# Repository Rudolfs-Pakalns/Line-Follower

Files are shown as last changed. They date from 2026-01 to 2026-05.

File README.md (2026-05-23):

# Line Follower

## This project contains code and resources for a line-following robot.

## Contents
- STM32 code for line-following robot
- KiCad schematic and PCB design files
- 3D model of the robot chassis
- Bill of Materials (BOM) for components used

[Line Follower Rules](https://robotuskola.lv/wp-content/uploads/2025/10/linefollower-rules-lv.pdf)

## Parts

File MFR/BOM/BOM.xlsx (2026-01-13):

N.p.k. | Detaļas numurs | Komponente / apraksts | Cena, par 1.gab, Eur | Skaits | Cena kopā, Eur | Tiešsaiste | Datasheet
1 | SUD50N04-8M8P-4GE3 | Power MOSFET, N Channel, 40 V, 50 A, 8800 µohm, TO-252 (DPAK), Surface Mount | 0.763 | 3 | 2.29 | farnell.lv (https://lv.farnell.com/vishay/sud50n04-8m8p-4ge3/mosfet-n-ch-40v-50a-to252/dp/1794799) | datasheet (https://4donline.ihs.com/images/VipMasterIC/IC/VISH/VISH-S-A0009485304/VISH-S-A0009485304-1.pdf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)
2 | BCX56 | Bipolar (BJT) Single Transistor, NPN, 80 V, 1 A, 500 mW, SOT-89, Surface Mount | 0.455 | 5 | 2.28 | farnell.lv (https://lv.farnell.com/multicomp-pro/bcx56/transistor-npn-1a-80v-sot89/dp/1798047) | datasheet (https://www.farnell.com/datasheets/2861630.pdf)
3 | QRE1113GR | Reflective Photo Interrupter, Phototransistor, SMD Gull Wing, 5 mm, 50 mA, 5 Vr, 1.2 Vf | 0.626 | 10 | 6.26 | farnell.lv (https://lv.farnell.com/onsemi/qre1113/photo-interrupter-reflective/dp/2322565) | datasheet (https://www.farnell.com/datasheets/2298118.pdf)
4 | BZD27C6V2P-E3-08 | Zener Single Diode, BZD, 6.2 V, 800 mW, DO-219AB, 2 Pins, 150 °C, Surface Mount | 0.191 | 5 | 0.96 | farnell.lv (https://lv.farnell.com/vishay/bzd27c6v2p-e3-08/zener-diode-0-8w-6-2v-do-219ab/dp/2451494) | datasheet (https://4donline.ihs.com/images/VipMasterIC/IC/VISH/VISH-S-A0018268363/VISH-S-A0018268363-1.pdf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)
5 | MP008280 | LED, Green, SMD, 1206 [3216 Metric], 20 mA, 2.4 V, 575 nm | 0.178 | 5 | 0.89 | farnell.lv (https://lv.farnell.com/multicomp-pro/mp008280/led-green-70mcd-575nm-1206/dp/3796311) | datasheet (https://www.farnell.com/datasheets/3497877.pdf)
6 | 599-0210-007F | LED, Red, SMD, 1206 [3216 Metric], 20 mA, 2.1 V, 633 nm | 0.138 | 10 | 1.38 | farnell.lv (https://lv.farnell.com/dialight/599-0210-007f/led-red-29mcd-633nm-1206/dp/3548447) | datasheet (https://www.farnell.com/datasheets/3122976.pdf)
7 | MCP6001UT-I/OT | Operational Amplifier, Single, 1 Channels, 1 MHz, 0.6 V/µs, 1.8V to 6V, SOT-23 | 0.261 | 10 | 2.61 | farnell.lv (https://lv.farnell.com/microchip/mcp6001ut-i-ot/op-amp-cmos-1mhz-1-8v-smd-6001/dp/8540845) | datasheet (https://www.farnell.com/datasheets/524878.pdf)
8 | TC33X-2-103E | Trimmer, Single Turn, Cermet, Top Adjust, 10 kohm, Surface Mount, 1 Turns | 0.231 | 10 | 2.31 | farnell.lv (https://lv.farnell.com/bourns/tc33x-2-103e/trimmer-10k-3mm/dp/1689863) | datasheet (https://4donline.ihs.com/images/VipMasterIC/IC/BOUR/BOUR-S-A0008387203/BOUR-S-A0008387203-1.pdf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)
9 | MCLRP12JTDSR200 | SMD Current Sense Resistor, 0.2 ohm, MC LRP Series, 2512 [6432 Metric], 2 W, ± 5%, Metal Strip | 0.23 | 10 | 2.3 | farnell.lv (https://lv.farnell.com/multicomp-pro/mclrp12jtdsr200/res-r2-5-2w-metal-strip-2512/dp/4067724) | datasheet (https://www.farnell.com/datasheets/3779528.pdf)
10 | LM2596DSADJG | DC-DC Switching Regulator, Buck, 4.5V to 40V in, 1.23V to 37V out, 3A out, TO-263-5 | 2.23 | 2 | 4.46 | farnell.lv (https://lv.farnell.com/onsemi/lm2596dsadjg/switching-regulator-buck-to-263/dp/2534162) | datasheet (https://4donline.ihs.com/images/VipMasterIC/IC/ONSM/ONSM-S-A0018752607/ONSM-S-A0018752677-1.pdf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)
11 | ATMEGA32U4-AU | MCU-Application Specific 8 bit, AVR MEGA, 16 MHz, 2.5 KB RAM/32 KB Program | 4.69 | 2 | 9.38 | farnell.lv (https://lv.farnell.com/microchip/atmega32u4-au/mcu-8bit-16mhz-tqfp-44/dp/1748525) | datasheet (https://ww1.microchip.com/downloads/en/DeviceDoc/Atmel-7766-8-bit-AVR-ATmega16U4-32U4_Datasheet.pdf)
12 | DRV8833PWPR | IC, MOTOR DRIVER, STEPPER, HTSSOP-16 | 2.56 | 2 | 5.12 | farnell.lv (https://lv.farnell.com/texas-instruments/drv8833pwpr/ic-motor-driver-stepper-htssop/dp/3118941) | datasheet (https://www.ti.com/lit/ds/symlink/drv8833.pdf?ts=1766103528152)
13 | SSA34-E3/5AT | Schottky Rectifier, 40 V, 3 A, Single, DO-214AC (SMA), 2 Pins, 490 mV | 0.17 | 3 | 0.51 | farnell.lv (https://lv.farnell.com/vishay/ssa34-e3-5at/schottky-rect-single-40v-do-214ac/dp/2889248) | datasheet (https://4donline.ihs.com/images/VipMasterIC/IC/VISH/VISH-S-A0010295301/VISH-S-A0010476739-1.pdf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)
14 | MCSJK-6F-16.00-20-30-40-B-30 | Crystal, 16 MHz, SMD, 7mm x 5mm, 30 ppm, 20 pF, 30 ppm, MP SJK 6F Series | 0.519 | 2 | 1.04 | farnell.lv (https://lv.farnell.com/multicomp-pro/mcsjk-6f-16-00-20-30-40-b-30/crystal-16mhz-20pf-7mm-x-5mm/dp/2854216) | datasheet (https://www.farnell.com/datasheets/3685747.pdf)
15 | C0805C200F1HACAUTO | SMD Multilayer Ceramic Capacitor, 20 pF, 100 V, 0805 [2012 Metric], ± 1%, X8R | 0.137 | 10 | 1.37 | farnell.lv (https://lv.farnell.com/kemet/c0805c200f1hacauto/capacitor-20pf-x8r-100v-0805/dp/4227805) | datasheet (https://content.kemet.com/datasheets/KEM_C1007_X8R_ULTRA_150C_SMD.pdf)
16 | EEEFP1V221AP | SMD Aluminium Electrolytic Capacitor, Radial Can - SMD, 220 µF, 35 V, 0.08 ohm | 0.781 | 3 | 2.34 | farnell.lv (https://lv.farnell.com/panasonic/eeefp1v221ap/cap-220-f-35v-radial-smd/dp/1539514) | datasheet (https://www.farnell.com/datasheets/4557251.pdf)
17 | EEEFP1E471AP | SMD Aluminium Electrolytic Capacitor, Radial Can - SMD, 470 µF, 25 V, 0.06 ohm | 1.07 | 2 | 2.14 | farnell.lv (https://lv.farnell.com/panasonic/eeefp1e471ap/cap-470-f-25v-radial-smd/dp/1539511) | datasheet (https://www.farnell.com/datasheets/4557251.pdf)
18 | CRCW080510K0JNEAC | SMD Chip Resistor, 10 kohm, ± 5%, 125 mW, 0805 [2012 Metric], Thick Film | 0.0164 | 20 | 0.33 | farnell.lv (https://lv.farnell.com/vishay/crcw080510k0jneac/res-10k-5-0-125w-thick-film-0805/dp/4177714) | datasheet (https://4donline.ihs.com/images/VipMasterIC/IC/VISH/VISH-S-A0003599164/VISH-S-A0003599164-1.pdf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)
19 | CRCW080522R0JNEA | SMD Chip Resistor, 22 ohm, ± 5%, 250 mW, 0805 [2012 Metric], Thick Film, General Purpose | 0.0191 | 10 | 0.19 | farnell.lv (https://lv.farnell.com/vishay/crcw080522r0jnea/res-22r-5-0-125w-0805-thick-film/dp/4139775) | datasheet (https://4donline.ihs.com/images/VipMasterIC/IC/VISH/VISH-S-A0025774705/VISH-S-A0025774688-1.pdf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)
20 | ERJU06F5101V | SMD Chip Resistor, 5.1 kohm, ± 1%, 125 mW, 0805 [2012 Metric], Thick Film, Sulfur Resistant | 0.0435 | 10 | 0.44 | farnell.lv (https://lv.farnell.com/panasonic/erju06f5101v/res-5k1-1-0-125w-0805-thick-film/dp/2145533) | datasheet (https://4donline.ihs.com/images/VipMasterIC/IC/PANA/PANA-S-A0014609435/PANA-S-A0014609435-1.pdf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)

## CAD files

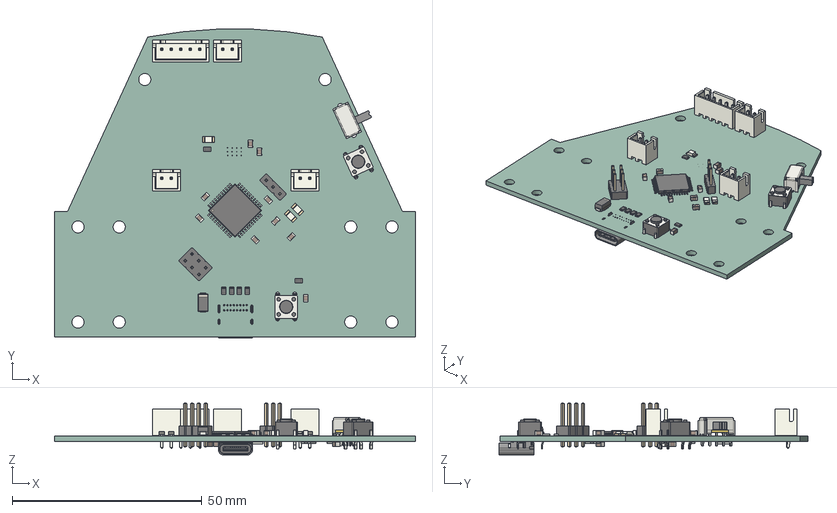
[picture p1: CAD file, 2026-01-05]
Line_Follower_PCBs/MCB/MCB-100-A/MCB-100-A.step
95.1 x 81.3 x 13.7 mm
C_0805_2012Metric x 12
R_0805_2012Metric x 10
JST_XH_B2B-XH-A_1x02_P2.50mm_Vertical x 3
LED_1206_3216Metric x 3
D_SMA
SW_PUSH_6mm_H4.3mm x 2
TQFP-44_10x10mm_P0.8mm
PinHeader_2x03_P2.54mm_Vertical
JST_XH_B5B-XH-A_1x05_P2.50mm_Vertical
PinHeader_1x03_P2.54mm_Vertical
SW_Slide_SPDT_Angled_CK_OS102011MA1Q
R_2512_6332Metric x 2
USB_C_Receptacle_GCT_USB4085
MCB-100-A_PCB

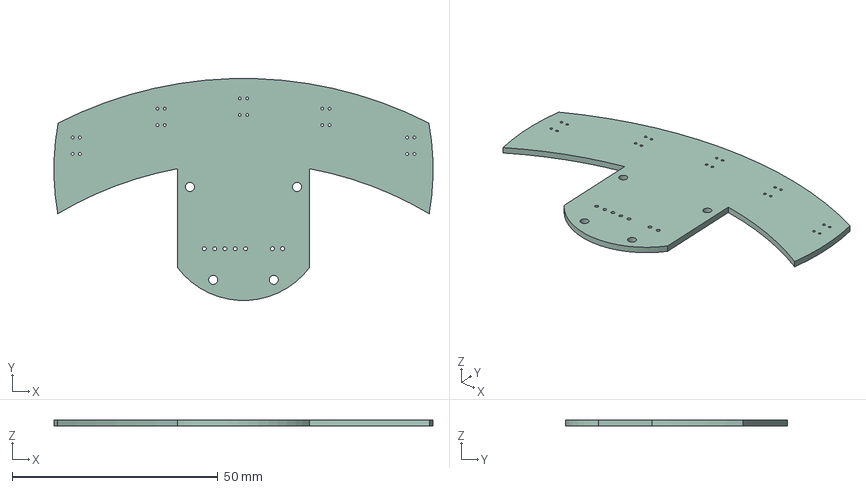
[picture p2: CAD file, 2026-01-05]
Line_Follower_PCBs/SMB/SMB-100-A/SMB-100-A.step
92.0 x 53.8 x 1.51 mm

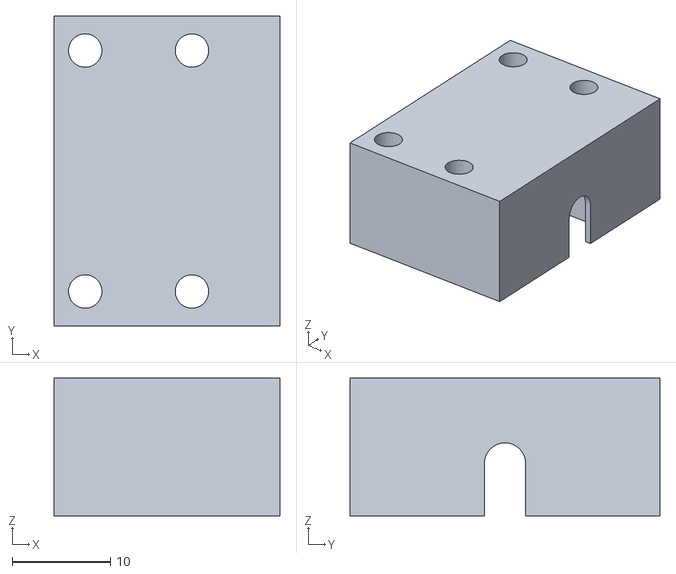
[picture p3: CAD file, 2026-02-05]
MFR/3D_Model/N20 Motor mount.stl
23.0 x 31.5 x 14.0

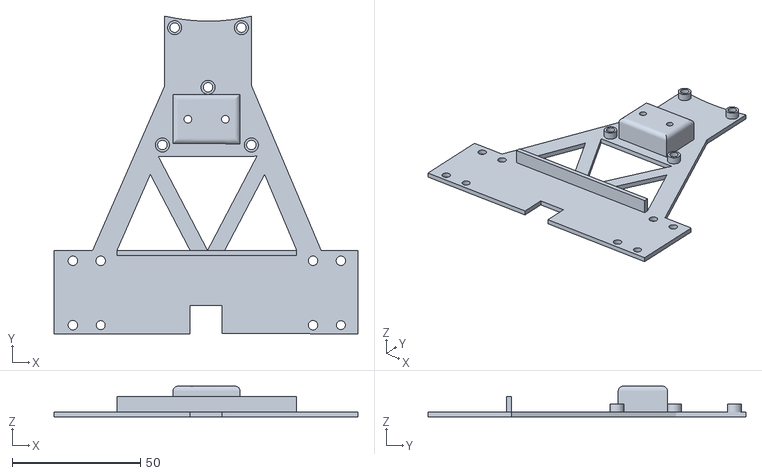
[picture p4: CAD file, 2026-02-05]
MFR/3D_Model/Chassis.stl
118.4 x 123.8 x 12.0

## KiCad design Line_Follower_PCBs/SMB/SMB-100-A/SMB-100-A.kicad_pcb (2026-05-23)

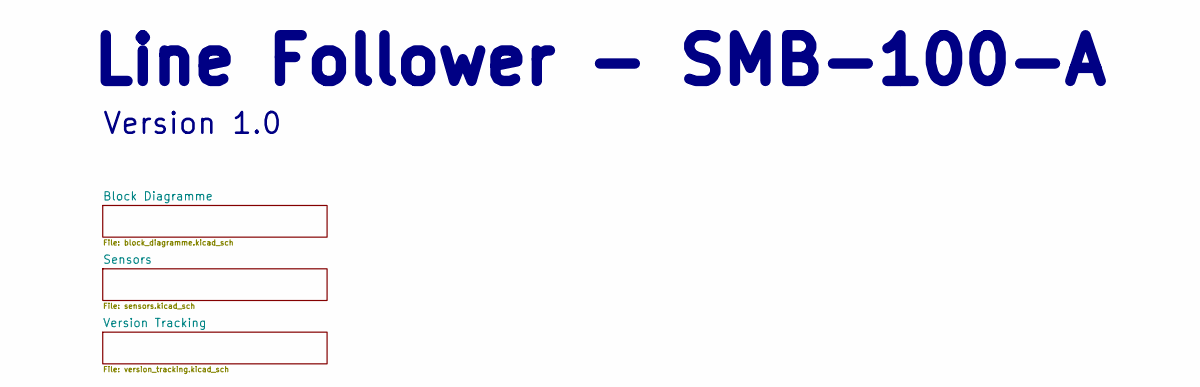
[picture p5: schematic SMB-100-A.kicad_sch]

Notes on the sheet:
Version 1.0
Line Follower - SMB-100-A

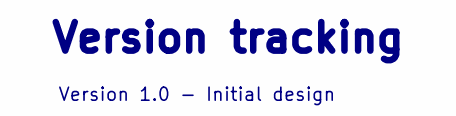
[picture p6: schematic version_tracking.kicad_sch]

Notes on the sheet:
Version 1.0 - Initial design
Version tracking

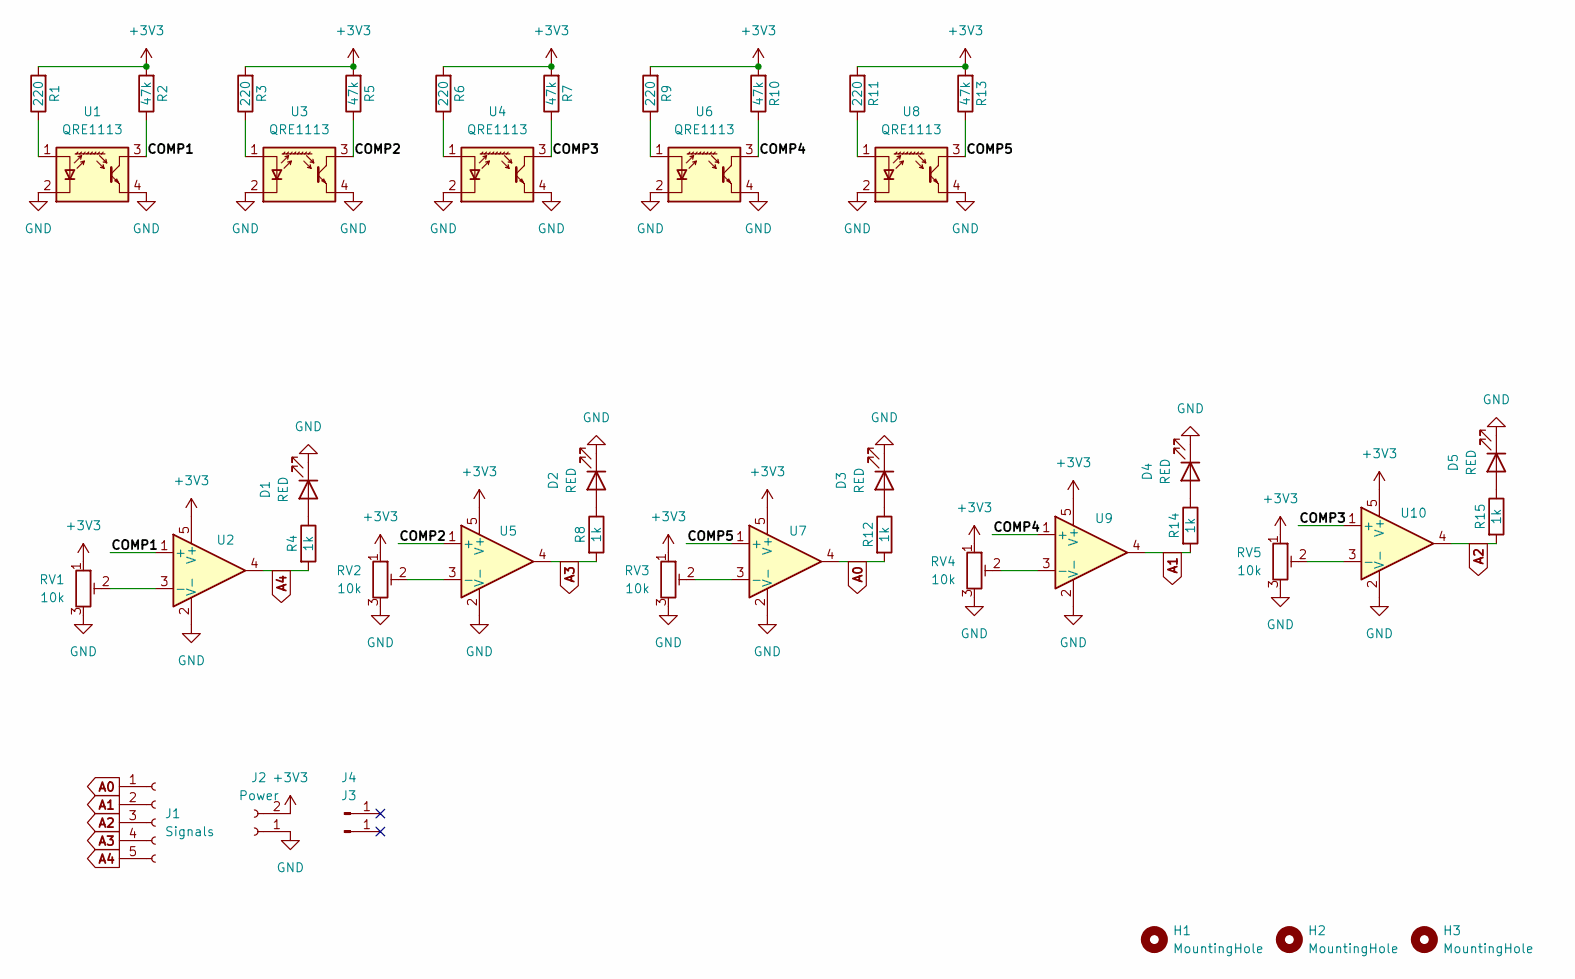
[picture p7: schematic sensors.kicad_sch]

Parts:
D1, D2, D3, D4, D5: RED; LED_1206_3216Metric
H1, H2, H3: MountingHole; MountingHole_3.2mm_M3
J1: Signals; JST_XH_B5B-XH-A_1x05_P2.50mm_Vertical
J2: Power; JST_XH_B2B-XH-A_1x02_P2.50mm_Vertical
J3, J4: Conn_01x01_Pin; PinHeader_1x01_P1.00mm_Vertical
R1, R3, R6, R9, R11: 220; R_0805_2012Metric_Pad1.20x1.40mm_HandSolder
R2, R5, R7, R10, R13: 47k; R_0805_2012Metric_Pad1.20x1.40mm_HandSolder
R4, R8, R12, R14, R15: 1k; R_0805_2012Metric_Pad1.20x1.40mm_HandSolder
RV1, RV2, RV3, RV4, RV5: 10k; Potentiometer_Bourns_TC33X_Vertical
U1, U3, U4, U6, U8: QRE1113; OnSemi_CASE100AQ
U2, U5, U7, U9, U10: MCP6001U; SOT-23-5_HandSoldering

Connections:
+3V3: J2.2, R1.2, R2.2, R3.2, R5.2, R6.2, R7.2, R9.2, R10.2, R11.2, R13.2, RV1.1, RV2.1, RV3.1, RV4.1, RV5.1, U2.5 (V+), U5.5 (V+), U7.5 (V+), U9.5 (V+), U10.5 (V+)
/Sensors/COMP1: R2.1, U1.3, U2.1 (+)
/Sensors/COMP2: R5.1, U3.3, U5.1 (+)
/Sensors/COMP3: R7.1, U4.3, U10.1 (+)
/Sensors/COMP4: R10.1, U6.3, U9.1 (+)
/Sensors/COMP5: R13.1, U7.1 (+), U8.3
A0: J1.1, R12.2, U7.4
A1: J1.2, R14.2, U9.4
A2: J1.3, R15.2, U10.4
A3: J1.4, R8.2, U5.4
A4: J1.5, R4.2, U2.4
GND: D1.1 (K), D2.1 (K), D3.1 (K), D4.1 (K), D5.1 (K), J2.1, RV1.3, RV2.3, RV3.3, RV4.3, RV5.3, U1.2 (K), U1.4, U2.2 (V-), U3.2 (K), U3.4, U4.2 (K), U4.4, U5.2 (V-), U6.2 (K), U6.4, U7.2 (V-), U8.2 (K), U8.4, U9.2 (V-), U10.2 (V-)
unnamed: D1.2 (A), R4.1
unnamed: D2.2 (A), R8.1
unnamed: D3.2 (A), R12.1
unnamed: D4.2 (A), R14.1
unnamed: D5.2 (A), R15.1
unnamed: R1.1, U1.1 (A)
unnamed: RV1.2, U2.3 (-)
unnamed: R3.1, U3.1 (A)
unnamed: R6.1, U4.1 (A)
unnamed: RV2.2, U5.3 (-)
unnamed: R9.1, U6.1 (A)
unnamed: RV3.2, U7.3 (-)
unnamed: R11.1, U8.1 (A)
unnamed: RV4.2, U9.3 (-)
unnamed: RV5.2, U10.3 (-)

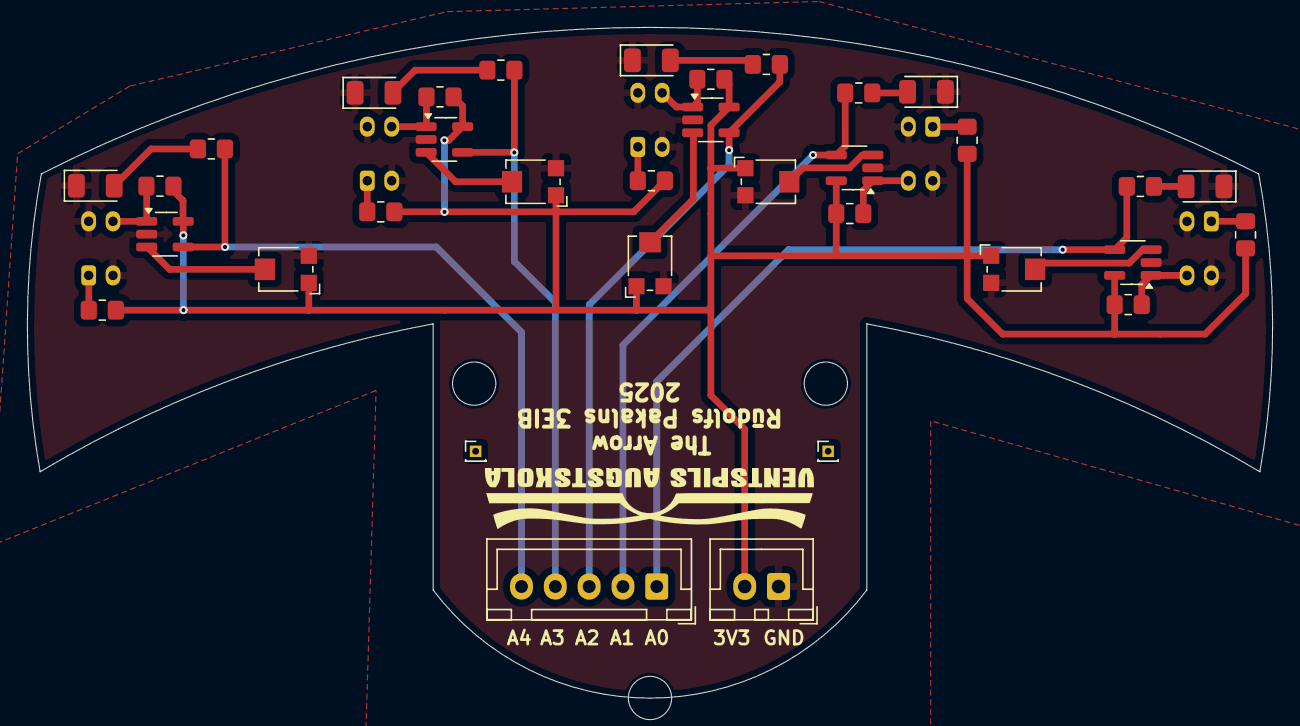
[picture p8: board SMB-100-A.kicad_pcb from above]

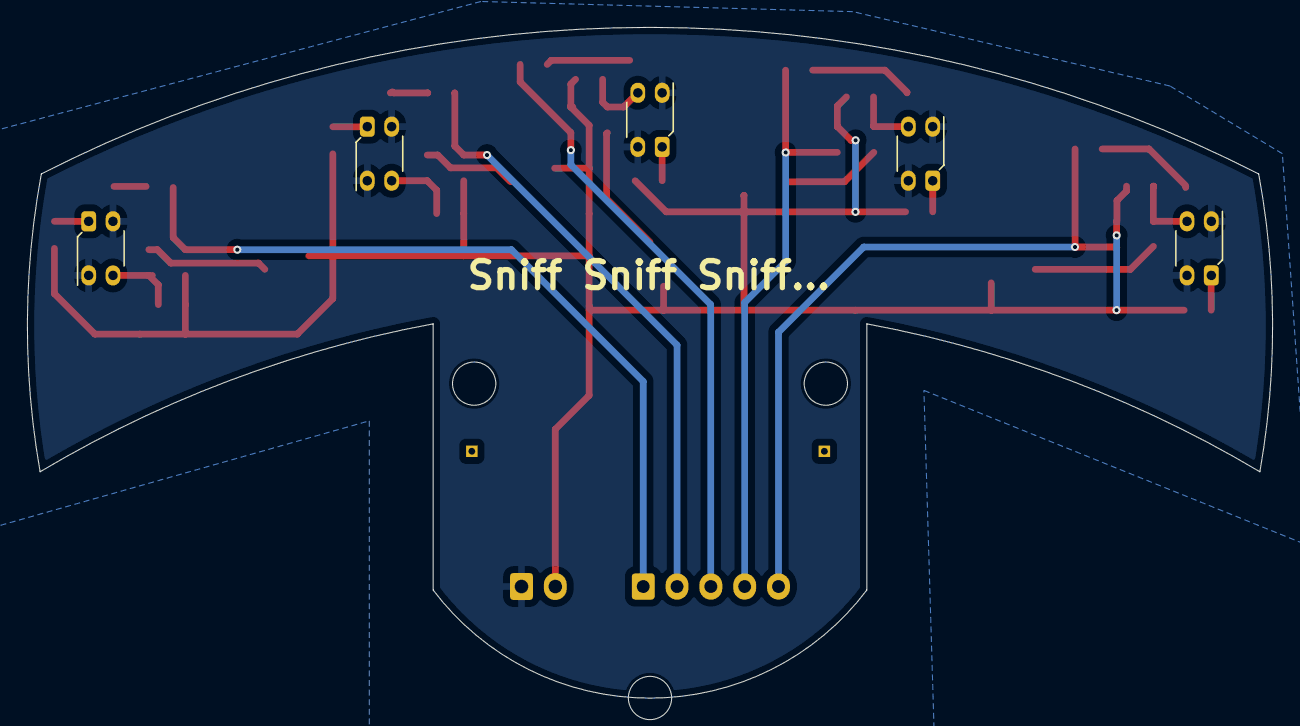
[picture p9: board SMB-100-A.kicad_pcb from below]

Board: 2 copper layers, 92.1 x 49.6 mm, 42 parts (5 on the bottom side), 27 nets.

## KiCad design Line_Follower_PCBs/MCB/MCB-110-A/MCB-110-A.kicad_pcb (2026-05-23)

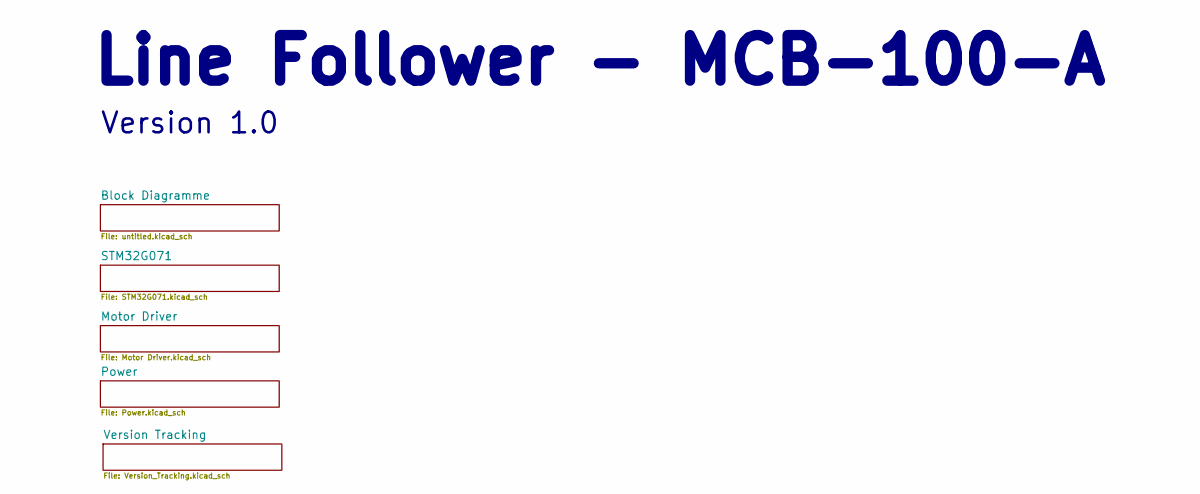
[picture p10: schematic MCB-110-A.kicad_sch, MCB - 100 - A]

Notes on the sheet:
Line Follower - MCB-100-A
Version 1.0


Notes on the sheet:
Version 1.0 - Initial design
Version tracking

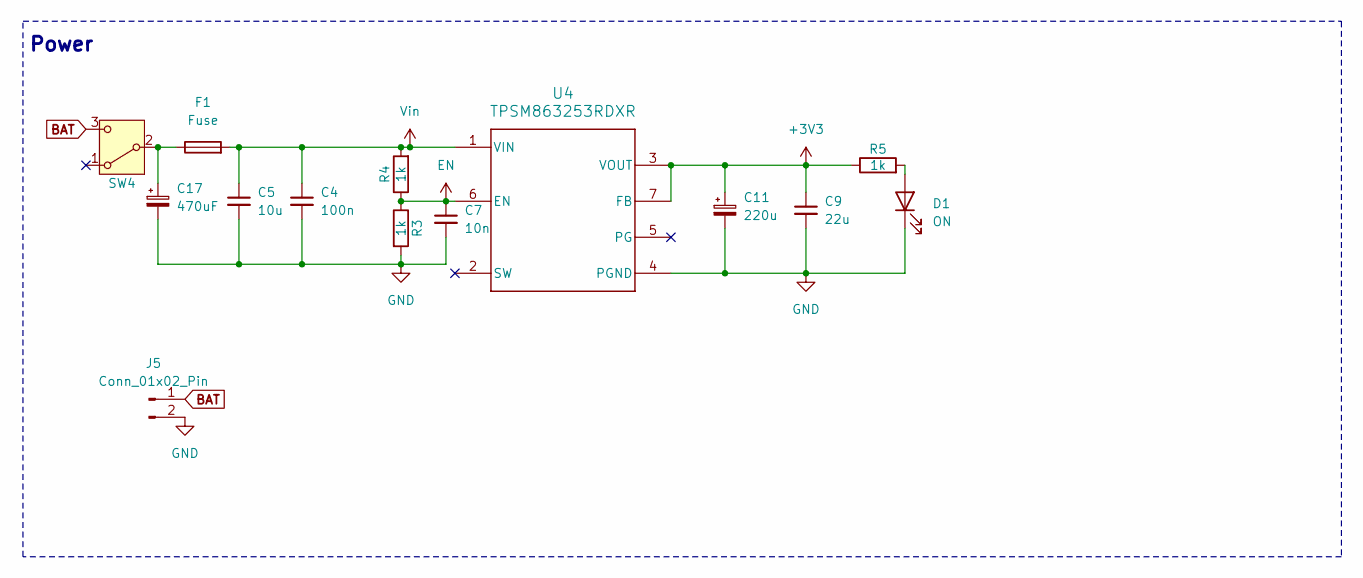
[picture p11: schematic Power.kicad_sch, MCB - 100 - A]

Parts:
C4: 100n; C_0805_2012Metric_Pad1.18x1.45mm_HandSolder
C5: 10u; C_0805_2012Metric_Pad1.18x1.45mm_HandSolder
C7: 10n; C_0805_2012Metric_Pad1.18x1.45mm_HandSolder
C9: 22u; C_0805_2012Metric_Pad1.18x1.45mm_HandSolder
C11: 220u; CP_Elec_8x10.5
C17: 470uF; CP_Elec_8x10.5
D1: ON; LED_1206_3216Metric
F1: Fuse; Fuse_Bourns_MF-RG300
J5: Conn_01x02_Pin; PinHeader_1x02_P2.54mm_Vertical
R3, R4, R5: 1k; R_0805_2012Metric_Pad1.20x1.40mm_HandSolder
SW4: SW_Nidec_CAS-120A1; SW_Slide_SPDT_Straight_CK_OS102011MS2Q
U4: TPSM863253RDXR; RDX0007A-MFG

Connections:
+3V3: C9.1, C11.1, R5.1, U4.3 (VOUT), U4.7 (FB); also elsewhere on the board
BAT: J5.1, SW4.3 (A); also elsewhere on the board
EN: C7.1, R3.1, R4.1, U4.6 (EN)
GND: C4.2, C5.2, C7.2, C9.2, C11.2, C17.2, D1.1 (K), J5.2, R3.2, U4.4 (PGND); also elsewhere on the board
unnamed: D1.2 (A), R5.2
unnamed: C17.1, F1.1, SW4.2 (B)
Vin: C4.1, C5.1, F1.2, R4.2, U4.1 (VIN)

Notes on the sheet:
Power

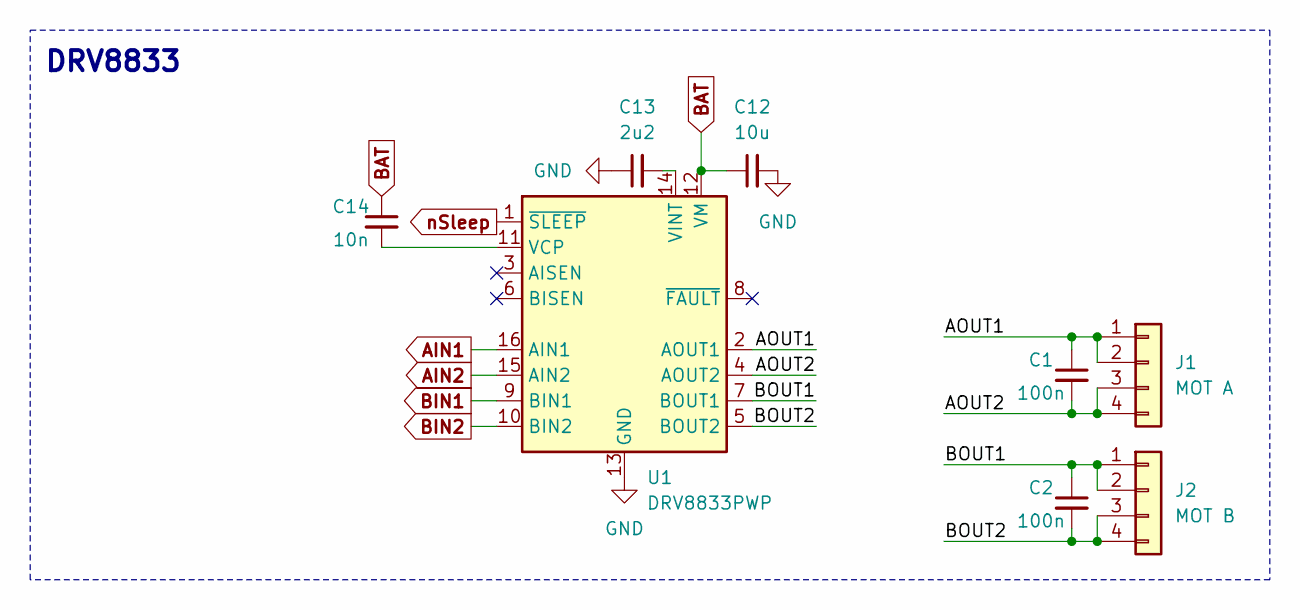
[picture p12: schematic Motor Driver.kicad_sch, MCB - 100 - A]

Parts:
C1, C2: 100n; C_0805_2012Metric_Pad1.18x1.45mm_HandSolder
C12: 10u; C_0805_2012Metric_Pad1.18x1.45mm_HandSolder
C13: 2u2; C_0805_2012Metric_Pad1.18x1.45mm_HandSolder
C14: 10n; C_0805_2012Metric_Pad1.18x1.45mm_HandSolder
J1: MOT A; PinHeader_1x04_P2.54mm_Vertical
J2: MOT B; PinHeader_1x04_P2.54mm_Vertical
U1: DRV8833PWP; HTSSOP-16-1EP_4.4x5mm_P0.65mm_EP3.4x5mm_Mask2.46x2.31mm_The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

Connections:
/Motor Driver/AOUT1: C1.1, J1.1, J1.2, U1.2 (AOUT1)
/Motor Driver/AOUT2: C1.2, J1.3, J1.4, U1.4 (AOUT2)
/Motor Driver/BOUT1: C2.1, J2.1, J2.2, U1.7 (BOUT1)
/Motor Driver/BOUT2: C2.2, J2.3, J2.4, U1.5 (BOUT2)
AIN1: U1.16 (AIN1); also elsewhere on the board
AIN2: U1.15 (AIN2); also elsewhere on the board
BAT: C12.1, C14.1, U1.12 (VM); also elsewhere on the board
BIN1: U1.9 (BIN1); also elsewhere on the board
BIN2: U1.10 (BIN2); also elsewhere on the board
GND: C12.2, C13.1, U1.13 (GND), U1.17 (GND); also elsewhere on the board
unnamed: C14.2, U1.11 (VCP)
unnamed: C13.2, U1.14 (VINT)
nSleep: U1.1 (~SLEEP); also elsewhere on the board

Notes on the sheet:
DRV8833

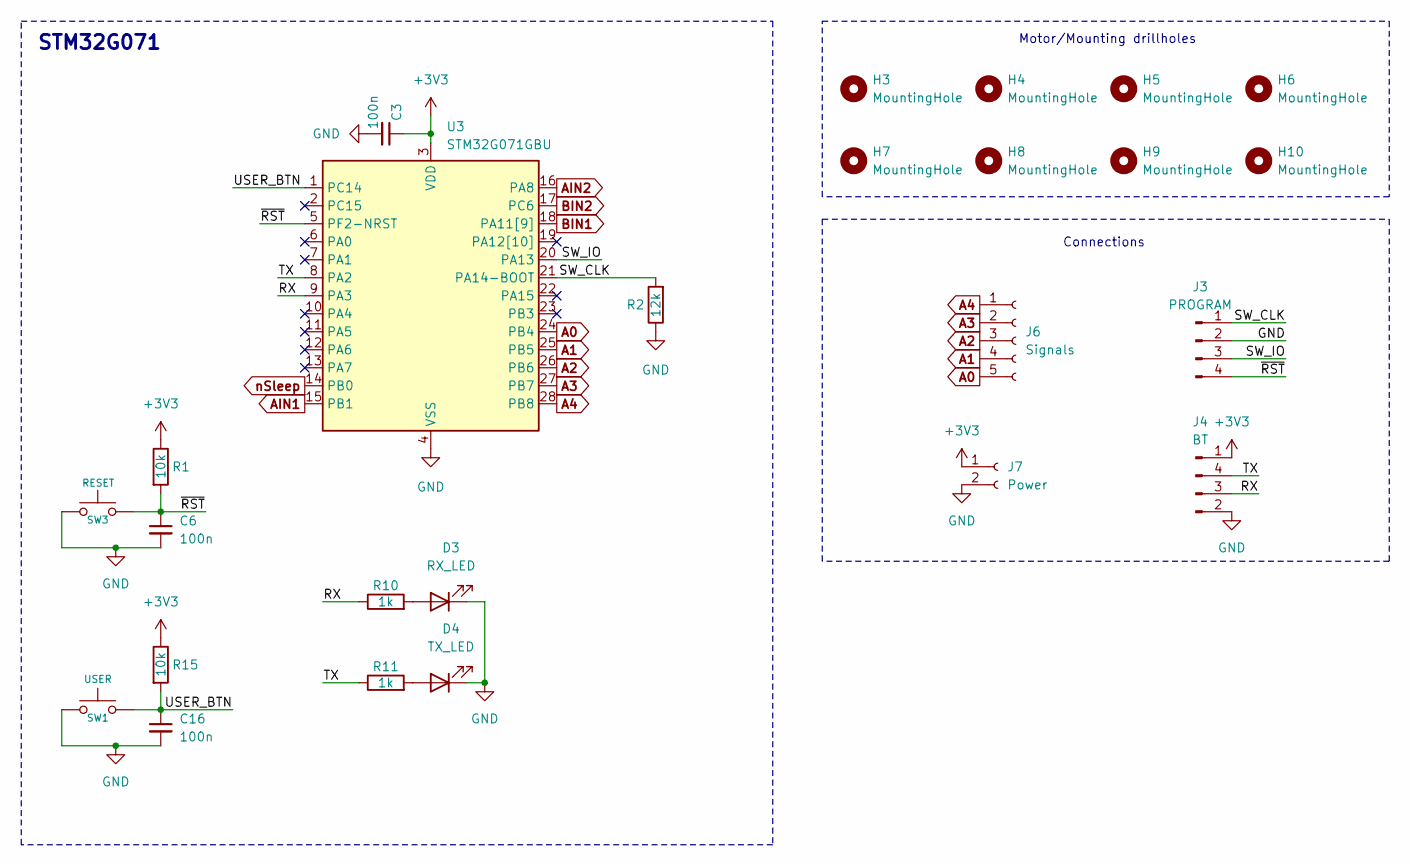
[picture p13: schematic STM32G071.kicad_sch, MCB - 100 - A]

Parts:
C3, C6, C16: 100n; C_0805_2012Metric_Pad1.18x1.45mm_HandSolder
D3: RX_LED; LED_1206_3216Metric
D4: TX_LED; LED_1206_3216Metric
H3, H4, H5, H6, H7, H8, H9, H10: MountingHole; MountingHole_3.2mm_M3
J3: PROGRAM; PinHeader_1x04_P2.54mm_Vertical
J4: BT; PinHeader_1x04_P2.54mm_Vertical
J6: Signals; JST_XH_B5B-XH-A_1x05_P2.50mm_Vertical
J7: Power; JST_XH_B2B-XH-A_1x02_P2.50mm_Vertical
R1, R15: 10k; R_0805_2012Metric_Pad1.20x1.40mm_HandSolder
R2: 12k; R_0805_2012Metric_Pad1.20x1.40mm_HandSolder
R10, R11: 1k; R_0805_2012Metric_Pad1.20x1.40mm_HandSolder
SW1: USER; SW_SPST_TL3305A
SW3: RESET; SW_SPST_TL3305A
U3: STM32G071GBU; QFN-28_4x4mm_P0.5mm

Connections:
+3V3: C3.1, J4.1, J7.1, R1.1, R15.1, U3.3 (VDD); also elsewhere on the board
/STM32G071/RX: J4.3, R10.1, U3.9 (PA3)
/STM32G071/SW_CLK: J3.1, R2.2, U3.21 (PA14-BOOT)
/STM32G071/SW_IO: J3.3, U3.20 (PA13)
/STM32G071/TX: J4.4, R11.1, U3.8 (PA2)
/STM32G071/USER_BTN: C16.1, R15.2, SW1.2, U3.1 (PC14)
/STM32G071/~RST: C6.1, J3.4 (Pin_2), R1.2, SW3.2, U3.5 (PF2-NRST)
A0: J6.5, U3.24 (PB4)
A1: J6.4, U3.25 (PB5)
A2: J6.3, U3.26 (PB6)
A3: J6.2, U3.27 (PB7)
A4: J6.1, U3.28 (PB8)
AIN1: U3.15 (PB1); also elsewhere on the board
AIN2: U3.16 (PA8); also elsewhere on the board
BIN1: U3.18 (PA11[9]); also elsewhere on the board
BIN2: U3.17 (PC6); also elsewhere on the board
GND: C3.2, C6.2, C16.2, D3.1 (K), D4.1 (K), J3.2 (Pin_4), J4.2, J7.2, R2.1, SW1.1, SW3.1, U3.4 (VSS); also elsewhere on the board
unnamed: D3.2 (A), R10.2
unnamed: D4.2 (A), R11.2
nSleep: U3.14 (PB0); also elsewhere on the board

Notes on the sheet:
Motor/Mounting drillholes
Connections
STM32G071

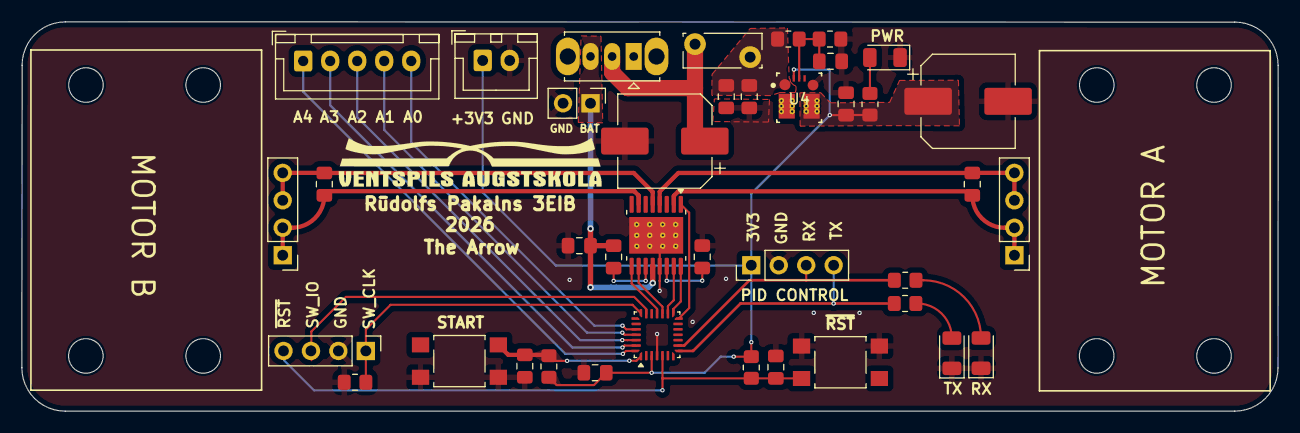
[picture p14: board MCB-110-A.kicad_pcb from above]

Board: 2 copper layers, 116.2 x 36.0 mm, 47 parts (0 on the bottom side), 31 nets.

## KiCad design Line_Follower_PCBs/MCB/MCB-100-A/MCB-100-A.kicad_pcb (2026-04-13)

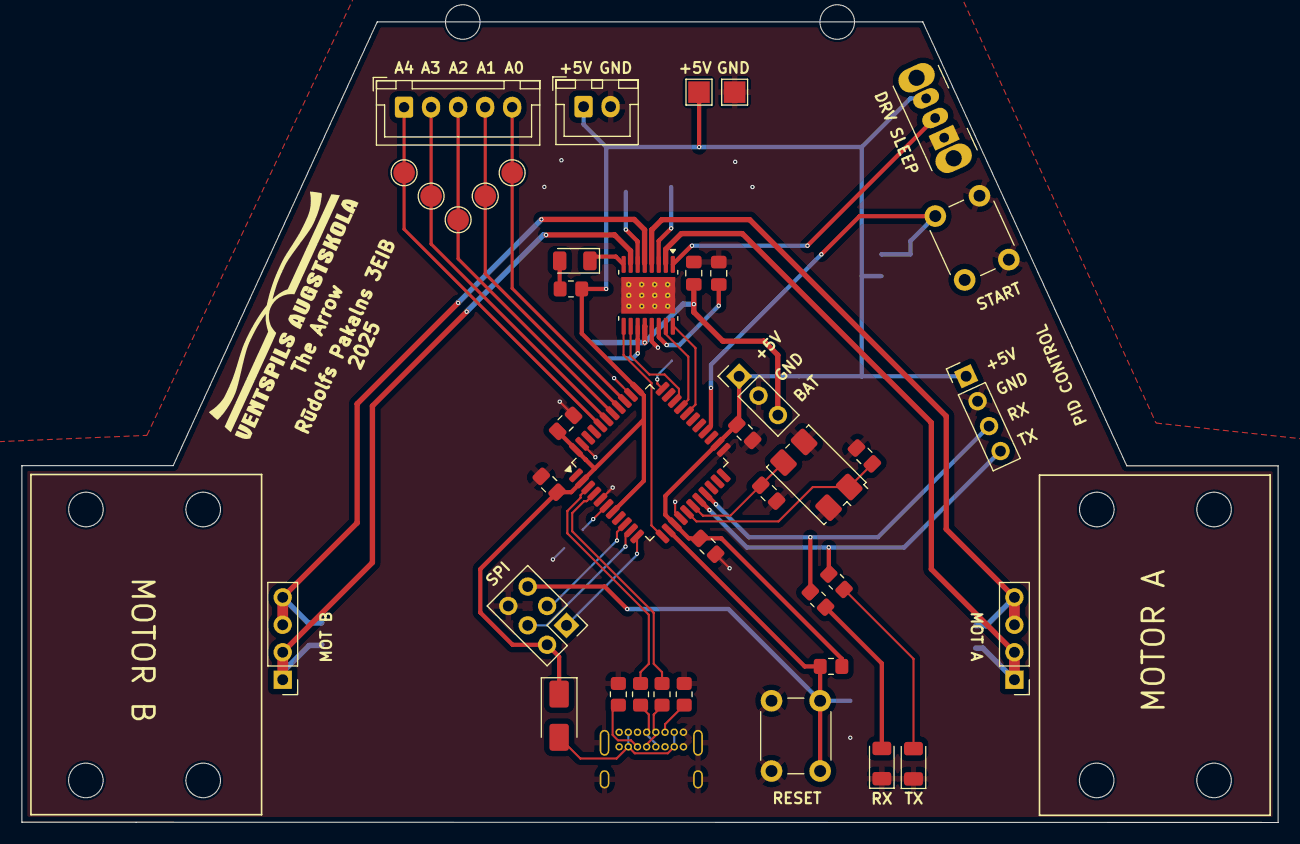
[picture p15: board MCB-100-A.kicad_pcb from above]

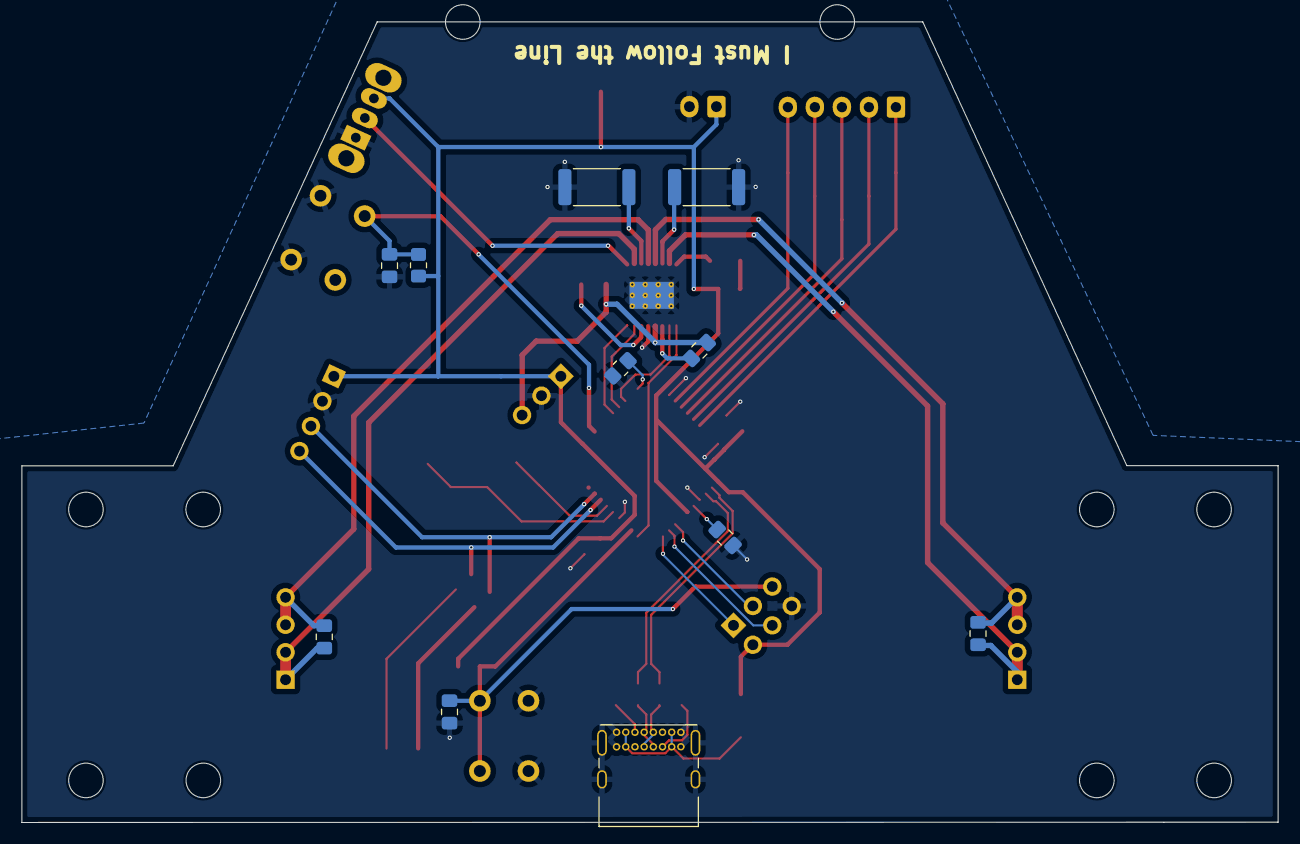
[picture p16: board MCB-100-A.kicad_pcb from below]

Board: 2 copper layers, 116.2 x 74.1 mm, 61 parts (11 on the bottom side), 43 nets.

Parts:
A1, A2, A3, A4, A5: TestPoint; TestPoint_Pad_D2.0mm
C1, C1#2, C2, C2#2, C3, C6, C15, C16: 100n; C_0805_2012Metric_Pad1.18x1.45mm_HandSolder
C4, C5: 20p; C_0805_2012Metric_Pad1.18x1.45mm_HandSolder
C7: 1u; C_0805_2012Metric_Pad1.18x1.45mm_HandSolder
C12: 10u; C_0805_2012Metric_Pad1.18x1.45mm_HandSolder
C13: 2u2; C_0805_2012Metric_Pad1.18x1.45mm_HandSolder
C14: 10n; C_0805_2012Metric_Pad1.18x1.45mm_HandSolder
D3: RX_LED; LED_1206_3216Metric
D4: TX_LED; LED_1206_3216Metric
D5: FAULT; LED_1206_3216Metric
D12: D_Schottky; D_SMA
H1, H2, H3, H4, H5, H6, H7, H8, H9, H10: MountingHole; MountingHole_3.2mm_M3
J1: MOT A; PinHeader_1x04_P2.54mm_Vertical
J2: MOT B; PinHeader_1x04_P2.54mm_Vertical
J3: USB_C_Receptacle_USB2.0_16P; USB_C_Receptacle_GCT_USB4085
J4: BT; PinHeader_1x04_P2.54mm_Vertical
J6: Signals; JST_XH_B5B-XH-A_1x05_P2.50mm_Vertical
J7: Power; JST_XH_B2B-XH-A_1x02_P2.50mm_Vertical
J9: Conn_01x03_Pin; PinHeader_1x03_P2.54mm_Vertical
J14: SPI; PinHeader_2x03_P2.54mm_Vertical
R1, R4, R15: 10k; R_0805_2012Metric_Pad1.20x1.40mm_HandSolder
R2, R3: 22; R_0805_2012Metric_Pad1.20x1.40mm_HandSolder
R10, R11, R12: 1k; R_0805_2012Metric_Pad1.20x1.40mm_HandSolder
R13, R14: 0.2; R_2512_6332Metric
R31, R32: 5k1; R_0805_2012Metric_Pad1.20x1.40mm_HandSolder
SW1: USER; SW_PUSH_6mm_H4.3mm
SW2: Sl_En; SW_Slide_SPDT_Angled_CK_OS102011MA1Q
SW3: RESET; SW_PUSH_6mm_H4.3mm
TP9, TP10: TestPoint; TestPoint_Pad_2.0x2.0mm
U1: DRV8833PWP; HTSSOP-16-1EP_4.4x5mm_P0.65mm_EP3.4x5mm_Mask2.46x2.31mm_The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
U2: ATmega32U4-A; TQFP-44_10x10mm_P0.8mm
Y1: Crystal_GND24; Crystal_SMD_FOX_FQ7050-4Pin_7.0x5.0mm

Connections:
+5V: C1.1, C2.1, C3.1, C15.1, D12.1 (K), J4.1, J7.1, J9.1, J14.2, R1.1, R12.2, R15.1, SW2.3 (A), TP9.1, U2.2 (UVCC), U2.7 (VBUS), U2.14 (VCC), U2.24 (AVCC), U2.34 (VCC), U2.44 (AVCC)
/ATmega32u4/D1+: J3.A6 (D+), J3.B6 (D+), R2.2
/ATmega32u4/D1-: J3.A7 (D-), J3.B7 (D-), R3.1
/ATmega32u4/D+: R2.1, U2.4 (D+)
/ATmega32u4/D-: R3.2, U2.3 (D-)
/ATmega32u4/MISO: J14.1, U2.11 (PB3)
/ATmega32u4/MOSI: J14.4, U2.10 (PB2)
/ATmega32u4/RESET: C6.1, J14.5, R1.2, SW3.2, U2.13 (~RESET)
/ATmega32u4/RX: J4.3, R10.1, U2.19 (PD1)
/ATmega32u4/SCK: J14.3, U2.9 (PB1)
/ATmega32u4/TX: J4.4, R11.1, U2.18 (PD0)
/ATmega32u4/USER_BTN: C16.1, R15.2, SW1.2, U2.26 (PD6)
/ATmega32u4/XTAL1: C5.1, U2.17 (XTAL1), Y1.3
/ATmega32u4/XTAL2: C4.1, U2.16 (XTAL2), Y1.1
/Motor Driver/AOUT1: C1#2.1, J1.1, J1.2, U1.2 (AOUT1)
/Motor Driver/AOUT2: C1#2.2, J1.3, J1.4, U1.4 (AOUT2)
/Motor Driver/ASEN: R13.1, U1.3 (AISEN)
/Motor Driver/BOUT1: C2#2.1, J2.1, J2.2, U1.7 (BOUT1)
/Motor Driver/BOUT2: C2#2.2, J2.3, J2.4, U1.5 (BOUT2)
/Motor Driver/BSEN: R14.1, U1.6 (BISEN)
/Motor Driver/Sleep: SW2.2 (B), U1.1 (~SLEEP)
A0: A4.1, J6.5, U2.36 (PF7)
A1: A3.1, J6.4, U2.37 (PF6)
A2: A5.1, J6.3, U2.38 (PF5)
A3: A2.1, J6.2, U2.39 (PF4)
A4: A1.1, J6.1, U2.40 (PF1)
BAT: C12.1, C14.1, J9.3, U1.12 (VM)
D5: U1.10 (BIN2), U2.31 (PC6)
D9: U1.16 (AIN1), U2.29 (PB5)
D10: U1.15 (AIN2), U2.30 (PB6)
D11: U1.9 (BIN1), U2.12 (PB7)
GND: C1.2, C2.2, C3.2, C4.2, C5.2, C6.2, C7.2, C12.2, C13.1, C15.2, C16.2, D3.1 (K), D4.1 (K), J3.A1 (GND), J3.A12 (GND), J3.B1 (GND), J3.B12 (GND), J3.S1 (SHIELD), J4.2, J7.2, J9.2, J14.6, R4.2, R13.2, R14.2, R31.2, R32.2, SW1.1, SW2.1 (C), SW3.1, TP10.1, U1.13 (GND), U1.17 (GND), U2.5 (UGND), U2.15 (GND), U2.23 (GND), U2.35 (GND), U2.43 (GND), Y1.2, Y1.4
unnamed: D3.2 (A), R10.2
unnamed: D4.2 (A), R11.2
unnamed: D5.2 (A), R12.1
unnamed: D5.1 (K), U1.8 (~FAULT)
unnamed: D12.2 (A), J3.A4 (VBUS), J3.A9 (VBUS), J3.B4 (VBUS), J3.B9 (VBUS)
unnamed: J3.A5 (CC1), R31.1
unnamed: J3.B5 (CC2), R32.1
unnamed: C14.2, U1.11 (VCP)
unnamed: C13.2, U1.14 (VINT)
unnamed: C7.1, U2.6 (UCAP)
unnamed: R4.1, U2.33 (~HWB/PE2)

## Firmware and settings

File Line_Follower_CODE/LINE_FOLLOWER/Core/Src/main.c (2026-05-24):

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
/* Includes ------------------------------------------------------------------*/
#include "main.h"

/* USER CODE BEGIN Includes */

#include "LF.h"
/* USER CODE END Includes */

/* USER CODE BEGIN PD */
#define MAX_SPEED 		65535
#define MIN_SPEED 		10000
#define BASE_SPEED 		22000

#define RX_BUFFER_SIZE 	16




/* USER CODE END PD */

TIM_HandleTypeDef htim1;
TIM_HandleTypeDef htim3;

UART_HandleTypeDef huart2;

/* USER CODE BEGIN PV */

// ==================================================================
/* PID STUFF */
float P = 1.0f;
float I = 0.0f;
float D = 0.0f;

float error = 0;
float previous_error = 0;

float integral = 0;
float derivative = 0;

float pid_output = 0;

float dt = 0.01f; // 10ms loop

uint16_t base_speed = BASE_SPEED;

// ==================================================================
/* UART */
uint8_t rx_byte;
char rx_buffer[RX_BUFFER_SIZE];

volatile uint16_t rx_index = 0;
volatile uint8_t rx_ready = 0;

// ==================================================================
/* SENSORS */
uint16_t sensors[ARRAY_SIZE] = {Sensor_1_Pin, Sensor_2_Pin, Sensor_3_Pin, Sensor_4_Pin, Sensor_5_Pin};
uint8_t sensor_values[ARRAY_SIZE] = {0};
int8_t sensor_weights[ARRAY_SIZE] = {-2, -1, 0, 1, 2};


/* USER CODE END PV */

void SystemClock_Config(void);
static void MX_GPIO_Init(void);
static void MX_TIM1_Init(void);
static void MX_TIM3_Init(void);
static void MX_USART2_UART_Init(void);
/**
  * @brief  The application entry point.
  * @retval int
  */
int main(void)
{

  /* MCU Configuration--------------------------------------------------------*/

  /* Reset of all peripherals, Initializes the Flash interface and the Systick. */
  HAL_Init();

  /* Configure the system clock */
  SystemClock_Config();

  /* Initialize all configured peripherals */
  MX_GPIO_Init();
  MX_TIM1_Init();
  MX_TIM3_Init();
  MX_USART2_UART_Init();
  /* USER CODE BEGIN 2 */
  HAL_UART_Receive_IT(&huart2, &rx_byte, 1);

  HAL_GPIO_WritePin(nSleep_GPIO_Port, nSleep_Pin, GPIO_PIN_SET);

  HAL_TIM_PWM_Start(&htim1, TIM_CHANNEL_1);
  HAL_TIM_PWM_Start(&htim1, TIM_CHANNEL_4);

  HAL_TIM_PWM_Start(&htim3, TIM_CHANNEL_1);
  HAL_TIM_PWM_Start(&htim3, TIM_CHANNEL_4);



  /* USER CODE END 2 */

  /* Infinite loop */
  /* USER CODE BEGIN WHILE */
  while (1)
  {

	  int32_t left_speed;
	  int32_t right_speed;

	  //uint8_t start = HAL_GPIO_ReadPin(Start_GPIO_Port, Start_Pin);

	  if(rx_ready)
	  {
		  cmd_service(rx_buffer, &P, &I, &D, &base_speed);
		  rx_ready = 0;
	  }


	  /* PID CALCULATIONS */
	  error = read_sensors(sensors, sensor_values, sensor_weights, &previous_error);
	  integral += error * dt;

	  if(integral > 100) integral = 100;

	  if(integral < -100) integral = -100;

	  derivative = (error - previous_error) / dt;
	  pid_output = (P * error) + (I * integral) + (D * derivative);
	  previous_error = error;

	  if(pid_output > MAX_SPEED) pid_output = MAX_SPEED;
	  if(pid_output < -MAX_SPEED) pid_output = -MAX_SPEED;


	  /* SPEED APLICATION */
	  left_speed  = base_speed + (int32_t)pid_output;
	  right_speed = base_speed - (int32_t)pid_output;

	  if(left_speed > MAX_SPEED) left_speed = MAX_SPEED;
	  if(left_speed < -MAX_SPEED)  left_speed = -MAX_SPEED;
	  if(right_speed > MAX_SPEED)right_speed = MAX_SPEED;
	  if(right_speed < -MAX_SPEED)right_speed = -MAX_SPEED;

	  set_left_motor(left_speed);
	  set_right_motor(right_speed);

	  HAL_Delay(10);

    /* USER CODE END WHILE */

    /* USER CODE BEGIN 3 */
  }
  /* USER CODE END 3 */
}

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
/* USER CODE BEGIN 4 */
void HAL_UART_RxCpltCallback(UART_HandleTypeDef *huart)
{
    static uint8_t receiving = 0;


    if(huart->Instance == USART2)
    {
        // ignore CR
        if(rx_byte == '\r')
        {
        }

        // message finished
        else if(rx_byte == '\n')
        {
            rx_buffer[rx_index] = '\0';

            rx_ready = 1;

            receiving = 0;
        }

        else
        {
            // first character of new message
            if(receiving == 0)
            {
                memset(rx_buffer, 0, sizeof(rx_buffer));
                rx_index = 0;

                receiving = 1;
            }

            // store character
            if(rx_index < RX_BUFFER_SIZE - 1)
            {
                rx_buffer[rx_index++] = rx_byte;
            }
        }

        HAL_UART_Receive_IT(&huart2, &rx_byte, 1);
    }
}




/* USER CODE END 4 */
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


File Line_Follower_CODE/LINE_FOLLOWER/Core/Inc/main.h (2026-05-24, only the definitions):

#define Start_Pin GPIO_PIN_14
#define Start_GPIO_Port GPIOC
#define nSleep_Pin GPIO_PIN_0
#define nSleep_GPIO_Port GPIOB
#define AIN1_Pin GPIO_PIN_1
#define AIN1_GPIO_Port GPIOB
#define AIN2_Pin GPIO_PIN_8
#define AIN2_GPIO_Port GPIOA
#define BIN2_Pin GPIO_PIN_6
#define BIN2_GPIO_Port GPIOC
#define BIN1_Pin GPIO_PIN_11
#define BIN1_GPIO_Port GPIOA
#define Sensor_1_Pin GPIO_PIN_4
#define Sensor_1_GPIO_Port GPIOB
#define Sensor_2_Pin GPIO_PIN_5
#define Sensor_2_GPIO_Port GPIOB
#define Sensor_3_Pin GPIO_PIN_6
#define Sensor_3_GPIO_Port GPIOB
#define Sensor_4_Pin GPIO_PIN_7
#define Sensor_4_GPIO_Port GPIOB
#define Sensor_5_Pin GPIO_PIN_8
#define Sensor_5_GPIO_Port GPIOB

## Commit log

2025-12-15 Initial commit; added project
    [LF_PCB.kicad_pcb, LF_PCB.kicad_sch]
2025-12-15 made schematic; missing DRV8833
    [LF_PCB.kicad_pcb, LF_PCB.kicad_sch]
2025-12-15 Added a bunch of shit
    [ATmega32U4.kicad_sch, LF_PCB.kicad_pcb, LF_PCB.kicad_sch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]
2025-12-16 Started PCB
    [ATmega32U4.kicad_sch, LF_PCB.kicad_pcb, Motor_Driver.kicad_sch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]
2025-12-17 Completed schematic
    [ATmega32U4.kicad_sch, LF_PCB.kicad_pcb, Motor_Driver.kicad_sch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]
2025-12-19 Made PCB
    [ATmega32U4.kicad_sch, LF_PCB.kicad_pcb, Motor_Driver.kicad_sch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]
2025-12-20 seperated PCBs into 3 seperate files and updated README
    [ATmega32U4.kicad_sch, ATmega32u4.kicad_sch, LF_PCB.kicad_pcb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]
2026-01-05 more stuff
    [ATmega32u4.kicad_sch, MCB-100-A.kicad_pcb, MCB-100-A.step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]
2026-01-12 Updated schematic
    [ATmega32u4.kicad_sch, MCB-100-A.kicad_pcb, Motor Driver.kicad_sch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]
2026-01-13 Updates and stuff
    [ATmega32u4.kicad_sch, BOM.xlsx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]
2026-02-05 added new 3d design
    [Chassis.stl, N20 Motor mount.stl]
2026-03-17 Added somewhat ok code
    [ATmega32U4.kicad_sch, ATmega32u4.kicad_sch, LF_PCB.kicad_pcb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]
2026-03-19 Edit: updated RF schematic
2026-05-23 first commit; added project
    [MCB-100-A-B_Cu.gbr, MCB-100-A-B_Mask.gbr, MCB-100-A-B_Paste.gbr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]
2026-05-24 Updated code with test funcs
    [PSB-100-A.kicad_pcb, PSB-100-A.kicad_sch, PSB-100-A.step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]

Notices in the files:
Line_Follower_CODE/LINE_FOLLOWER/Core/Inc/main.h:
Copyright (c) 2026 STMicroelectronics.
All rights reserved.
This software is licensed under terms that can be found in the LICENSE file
